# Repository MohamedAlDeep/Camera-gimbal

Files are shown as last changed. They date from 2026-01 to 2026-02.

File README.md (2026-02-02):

# HL Camera Gimbal
This is 3-Axis camera gimbal capable of lifting medium weight mirrorless cameras thus the *HL (heavy lifter)*, this product features two intertial units eliminating fast movement drifting. 

> Why making this project?

First it is cooolll in my oppinion, second I found that this would be integrated into other future projects not with the same frame but with the pcb, also My brother owns a camera.

## Wiring Diagram
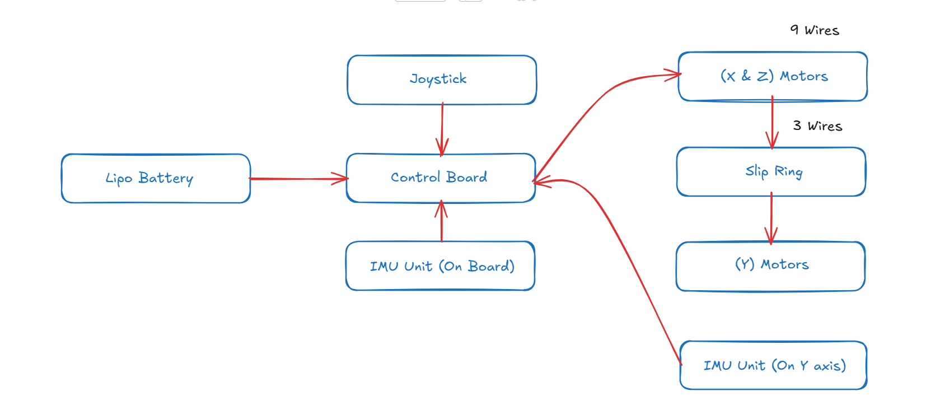
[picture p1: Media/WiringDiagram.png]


## BOM
| Name | Description | Link | Unit Price | Quantity | Total | Running Total |
|:---|:---|:---|---:|---:|---:|---:|
| Motors | Rctimer GBM5010-150T 90KV Gimbal Brushless Motor 5010 | [Link](https://ar.aliexpress.com/item/1005002552552208.html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) | 24.99 | 3 | 74.97 | 74.97 |
| Battery | 4S LiPo battery 7.4v  12000mAh 25C | [Link](https://ar.aliexpress.com/item/1005001565460048.html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) | 87.39 | 1 | 87.39 | 162.36 |
| Slip Ring | 5X22mm 6CH 2A | [Link](https://ar.aliexpress.com/item/1005008132607911.html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) | 21.86 | 1 | 21.86 | 184.22 |
| Pin Headers | 1.27mm1*10P Straight Pin header | [Link](https://jlcpcb.com/partdetail/29704-1_27mm1_10P_Straight_Pinheader/C28952) | 0.05 | 2 | 0.1  | 184.32 |
| LED | Small Led for indication | [Link](https://jlcpcb.com/partdetail/Hubei_KENTOElec-KT0603R/C2286) | 0.01 | 1 | 0.01 | 184.33 |
| Resistor 1KΩ | 1k ohm resistor | [Link](https://jlcpcb.com/partdetail/PANASONIC-EXBV4V102JV/C713466) | 0.04 | 3 | 0.12 | 184.45 |
| Resistor 45.3KΩ | 45.3KΩ ohm resistor | [Link](https://jlcpcb.com/partdetail/RALEC-RTT014532FTH/C166189) | 0.01 | 1 | 0.01 | 184.46 |
| Resistor 100KΩ | 100k ohms resistor | [Link](https://jlcpcb.com/partdetail/YAGEO-RC0603FR07100KL/C14675) | 0.01 | 1 | 0.01 | 184.47 |
| Resistor 10KΩ | 10k ohms resistor | [Link](https://jlcpcb.com/partdetail/16079-0603WAJ0103T5E/C15401) | 0.01 | 2 | 0.02 | 184.49 |
| Resistor 2.2KΩ | 2.2K ohms resistor | [Link](https://jlcpcb.com/partdetail/4597-0603WAF2201T5E/C4190) | 0.01 | 2 | 0.02 | 184.51 |
| Capacitor 100μF | 100 micro farads capacitor | [Link](https://jlcpcb.com/partdetail/3153-KM107M063F12RR0VH2FP0/C2772) | 0.05 | 3 | 0.15 | 184.66 |
| Capacitor 10μF | 10 micro farads capacitor | [Link](https://jlcpcb.com/partdetail/20411-CL10A106KP8NNNC/C19702) | 0.01 | 3 | 0.03 | 184.69 |
| Capacitor 0.1μF | 0.1 micro farads capacitor | [Link](https://jlcpcb.com/partdetail/YAGEO-CC0603KRX7R9BB104/C14663) | 0.01 | 3 | 0.03 | 184.72 |
| Toggle Button | Button | [Link](https://jlcpcb.com/partdetail/hanxia-HX_TS4540CJ_160gf022/C7463293) | 0.02 | 1 | 0.02 | 184.74 |
| Motor Drivers | DRV8313PWP | [Link](https://jlcpcb.com/partdetail/TexasInstruments-DRV8313PWPR/C92482) | 1.72 | 3 | 5.16 | 189.9  |
| STM32 Microcontroller | 128Kb memory flash MCU | [Link](https://jlcpcb.com/partdetail/STMicroelectronics-STM32G431CBT6/C529355) | 3.13 | 1 | 3.13 | 193.03 |
| Inductor 10μH | 10μH inductor | [Link](https://jlcpcb.com/partdetail/Sunlord-SDFL1608S100KTF/C1035) | 0.01 | 1 | 0.01 | 193.04 |
| Power converter | TPS54302 | [Link](https://jlcpcb.com/partdetail/TexasInstruments-TPS54302DDCR/C311983) | 0.15 | 1 | 0.15 | 193.19 |
| Inertial Units | ICM-20602 | [Link](https://jlcpcb.com/partdetail/TDKInvenSense-ICM20602/C97633) | 5.08 | 2 | 10.16 | 203.35 |
## Showcase

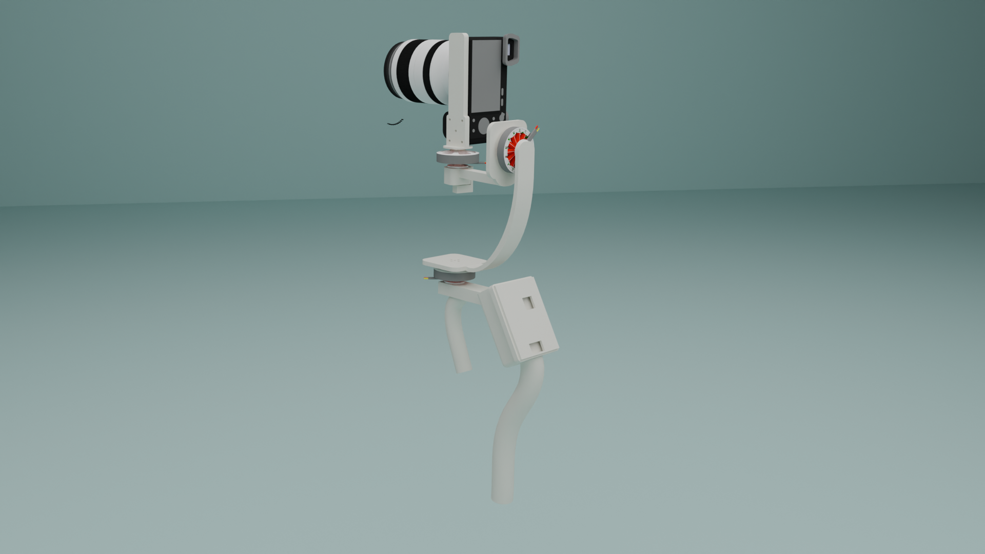
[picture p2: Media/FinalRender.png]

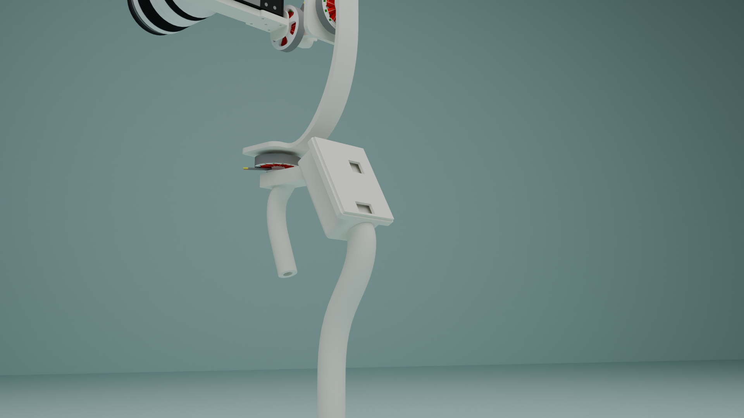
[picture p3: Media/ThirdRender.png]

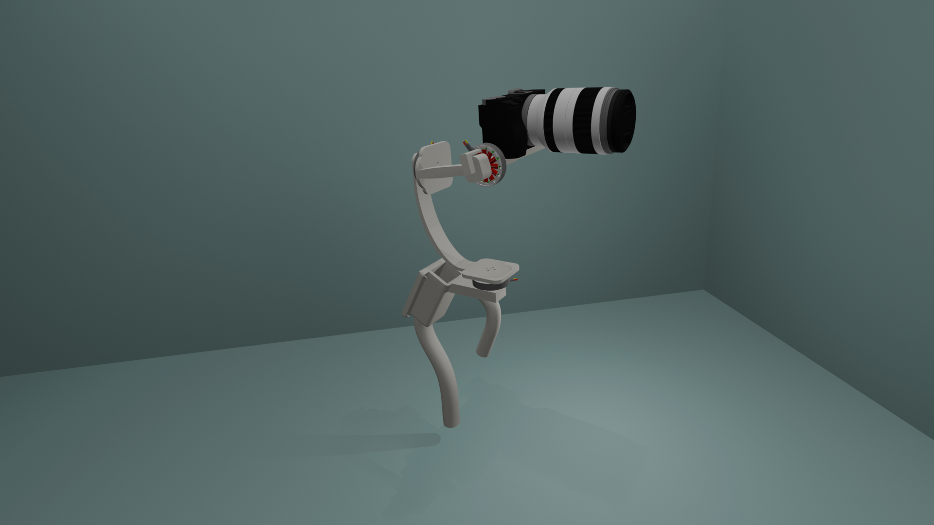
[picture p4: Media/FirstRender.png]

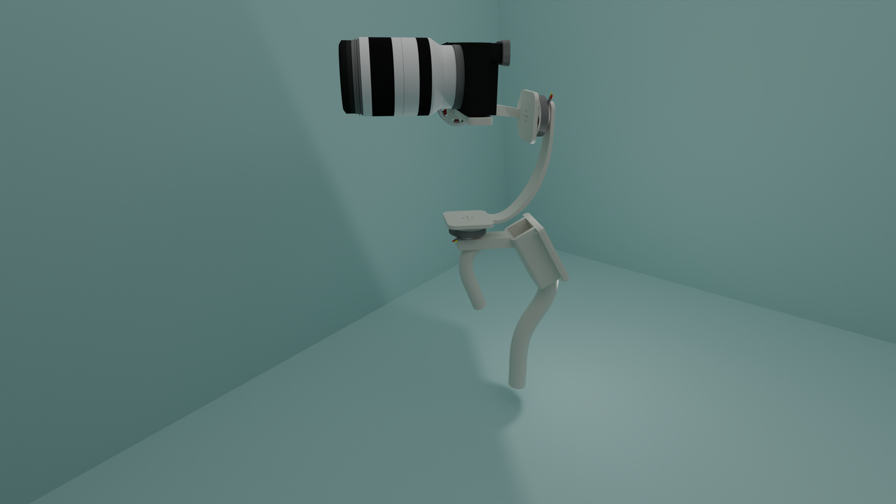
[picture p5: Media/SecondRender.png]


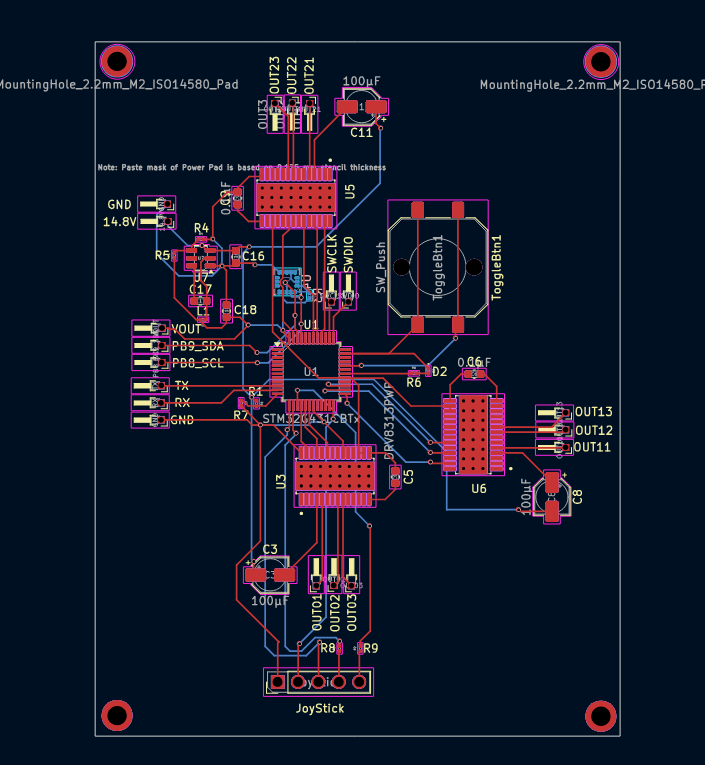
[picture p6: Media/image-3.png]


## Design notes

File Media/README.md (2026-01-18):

# HL Camera Gimbal
This is 3-Axis camera gimbal capable of lifting medium weight mirrorless cameras thus the *HL (heavy lifter)*, this product features two intertial units eliminating fast movement drifting. 

> Why making this project?

I found that this would be integrated into other future projects, also My brother owns a camera and.

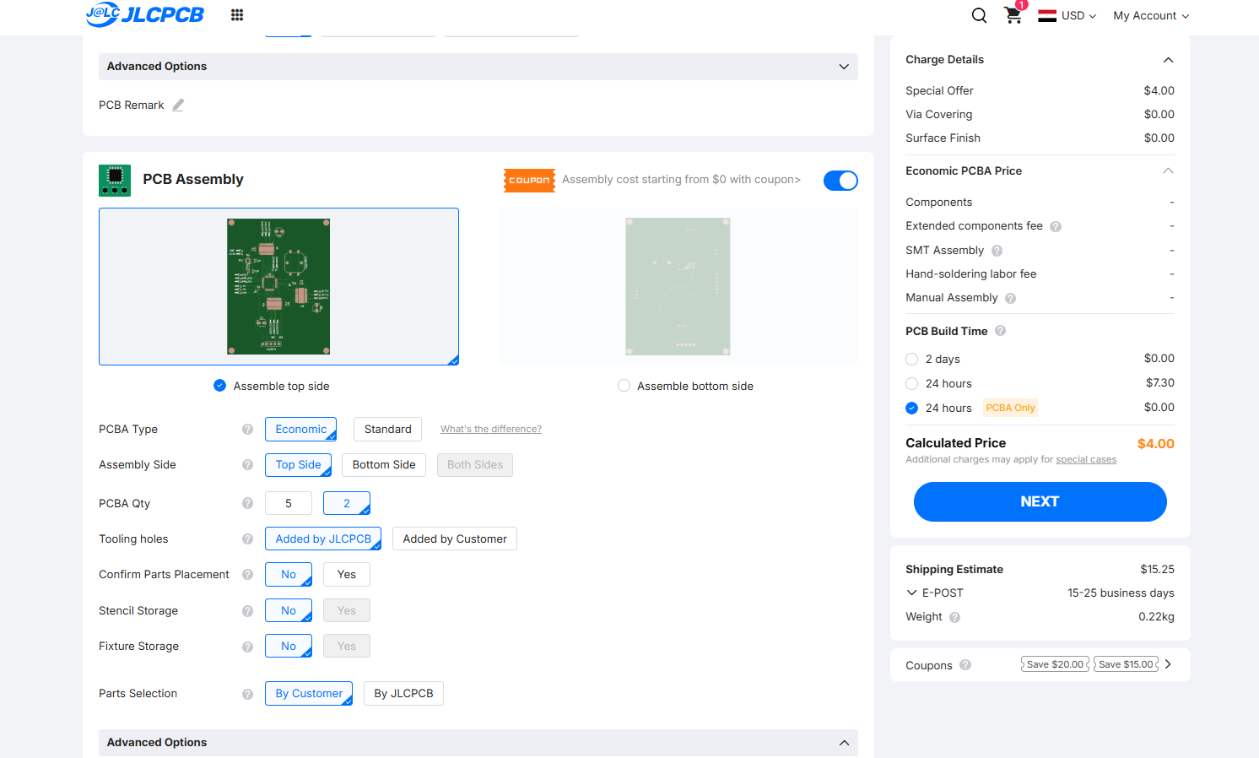
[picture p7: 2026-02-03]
Media/CARTS/JLC_PCB_CART.png

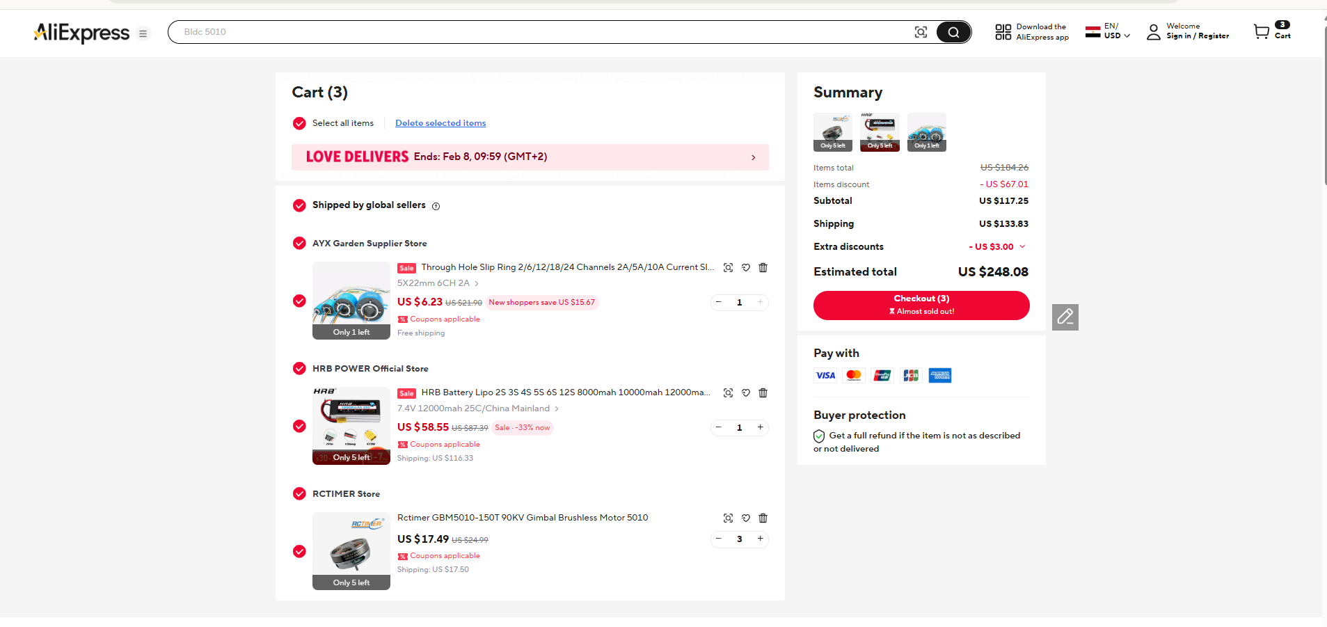
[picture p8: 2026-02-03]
Media/CARTS/AliExpressCart.png

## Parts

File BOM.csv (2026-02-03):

Name | Description | Link | Unit Price | Quantity | Total | Running Total
Motors | Rctimer GBM5010-150T 90KV Gimbal Brushless Motor 5010 | https://ar.aliexpress.com/item/1005002552552208.html?curPageLogUid=78YJsnV9XrQS | 24.99 | 3 | 74.97 | 74.97
Battery | 4S LiPo battery 7.4v 12000mAh 25C | https://ar.aliexpress.com/item/1005001565460048.html?curPageLogUid=I0zJC1hyaeP7 | 87.39 | 1 | 87.39 | 162.36
Slip Ring | 5X22mm 6CH 2A | https://ar.aliexpress.com/item/1005008132607911.html?curPageLogUid=WKGMTuvrKkpL | 21.86 | 1 | 21.86 | 184.22
Pin Headers | 1.27mm1*10P Straight Pin header | https://jlcpcb.com/partdetail/29704-1_27mm1_10P_Straight_Pinheader/C28952 | 0.05 | 2 | 0.1 | 184.32
LED | Small Led for indication | https://jlcpcb.com/partdetail/Hubei_KENTOElec-KT0603R/C2286 | 0.01 | 1 | 0.01 | 184.33
Resistor 1KΩ | 1k ohm resistor | https://jlcpcb.com/partdetail/PANASONIC-EXBV4V102JV/C713466 | 0.04 | 3 | 0.12 | 184.45
Resistor 45.3KΩ | 45.3KΩ ohm resistor | https://jlcpcb.com/partdetail/RALEC-RTT014532FTH/C166189 | 0.01 | 1 | 0.01 | 184.46
Resistor 100KΩ | 100k ohms resistor | https://jlcpcb.com/partdetail/YAGEO-RC0603FR07100KL/C14675 | 0.01 | 1 | 0.01 | 184.47
Resistor 10KΩ | 10k ohms resistor | https://jlcpcb.com/partdetail/16079-0603WAJ0103T5E/C15401 | 0.01 | 2 | 0.02 | 184.49
Resistor 2.2KΩ | 2.2K ohms resistor | https://jlcpcb.com/partdetail/4597-0603WAF2201T5E/C4190 | 0.01 | 2 | 0.02 | 184.51
Capacitor 100μF | 100 micro farads capacitor | https://jlcpcb.com/partdetail/3153-KM107M063F12RR0VH2FP0/C2772 | 0.05 | 3 | 0.15 | 184.66
Capacitor 10μF | 10 micro farads capacitor | https://jlcpcb.com/partdetail/20411-CL10A106KP8NNNC/C19702 | 0.01 | 3 | 0.03 | 184.69
Capacitor 0.1μF | 0.1 micro farads capacitor | https://jlcpcb.com/partdetail/YAGEO-CC0603KRX7R9BB104/C14663 | 0.01 | 3 | 0.03 | 184.72
Toggle Button | Button | https://jlcpcb.com/partdetail/hanxia-HX_TS4540CJ_160gf022/C7463293 | 0.02 | 1 | 0.02 | 184.74
Motor Drivers | DRV8313PWP | https://jlcpcb.com/partdetail/TexasInstruments-DRV8313PWPR/C92482 | 1.72 | 3 | 5.16 | 189.9
STM32 Microcontroller | 128Kb memory flash MCU | https://jlcpcb.com/partdetail/STMicroelectronics-STM32G431CBT6/C529355 | 3.13 | 1 | 3.13 | 193.03
Inductor 10μH | 10μH inductor | https://jlcpcb.com/partdetail/Sunlord-SDFL1608S100KTF/C1035 | 0.01 | 1 | 0.01 | 193.04
Power converter | TPS54302 | https://jlcpcb.com/partdetail/TexasInstruments-TPS54302DDCR/C311983 | 0.15 | 1 | 0.15 | 193.19
Inertial Units | ICM-20602 | https://jlcpcb.com/partdetail/TDKInvenSense-ICM20602/C97633 | 5.08 | 2 | 10.16 | 203.35
Delivery
PCB |  |  |  |  |  | 15.25
ALI Express |  |  |  |  |  | 133.8
Total |  |  |  |  |  | 352.4

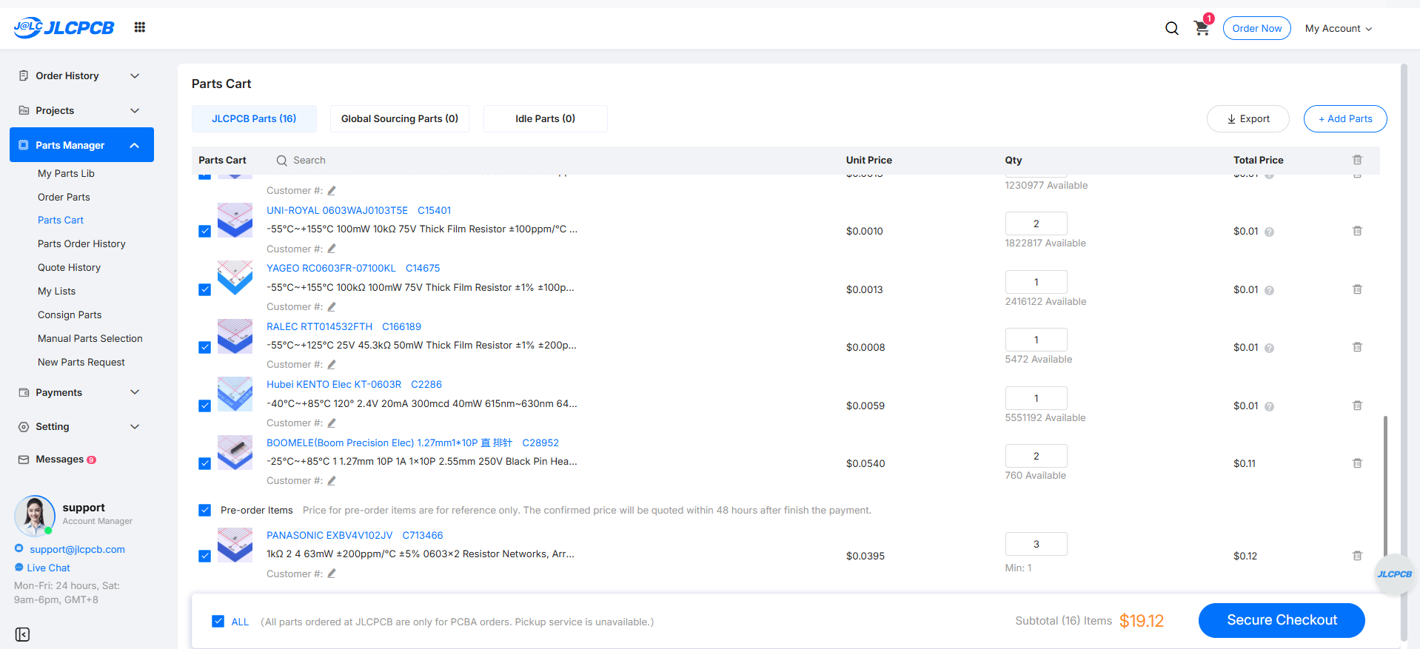
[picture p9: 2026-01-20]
Media/CARTS/JLC_Components_Cart.png

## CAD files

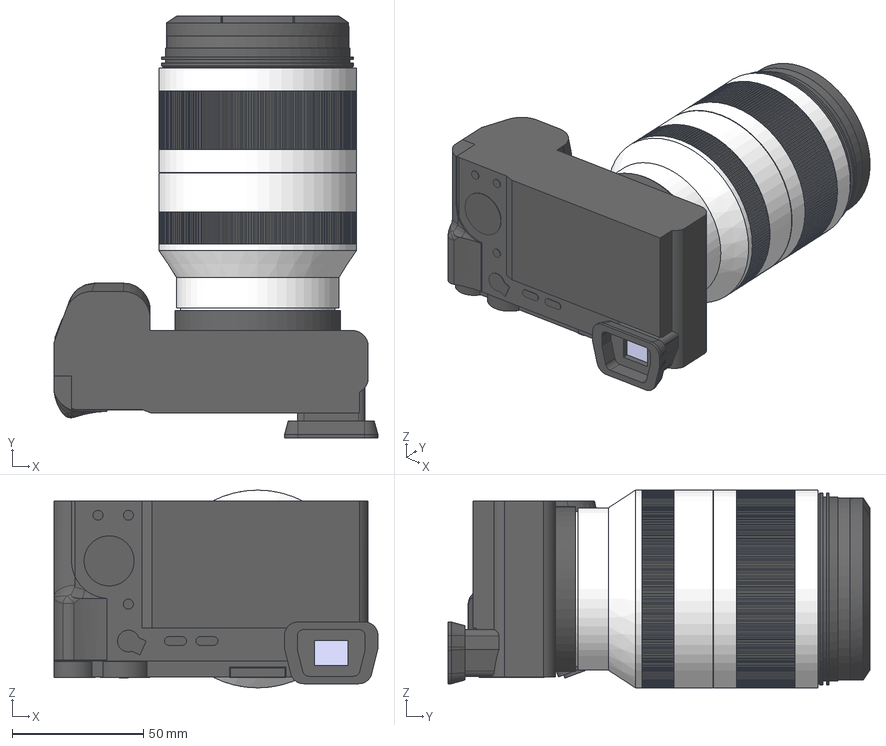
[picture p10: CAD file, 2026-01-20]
CAD/Prebuilt_Modules/A6300 18 200 Assembly.stp
123.2 x 160.4 x 75.2 mm
SEL 18 200
A6300
UV Filter
Lens Cap

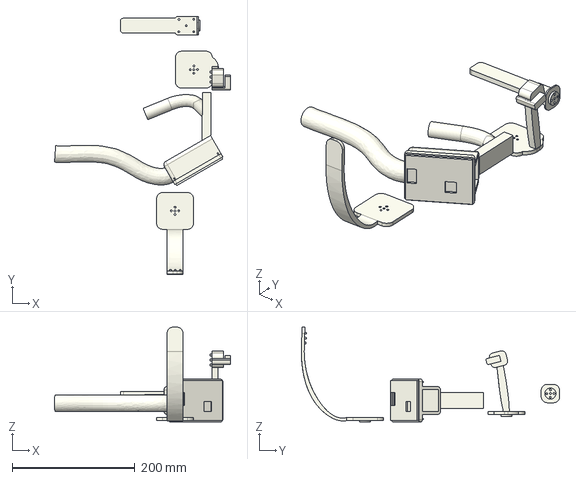
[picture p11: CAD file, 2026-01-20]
CAD/Frame_3DPrint.step
286.4 x 420.3 x 154.1 mm

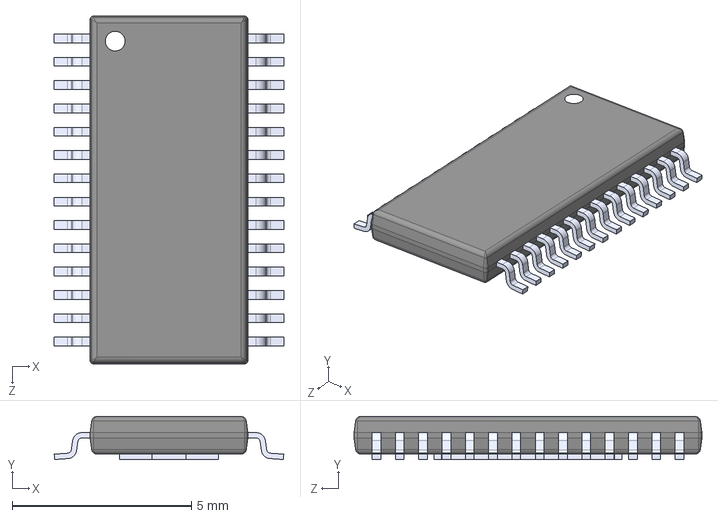
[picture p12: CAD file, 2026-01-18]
PCB/PrerequisitesFootprints/DRV8313PWP.step
6.40 x 1.20 x 9.70 mm

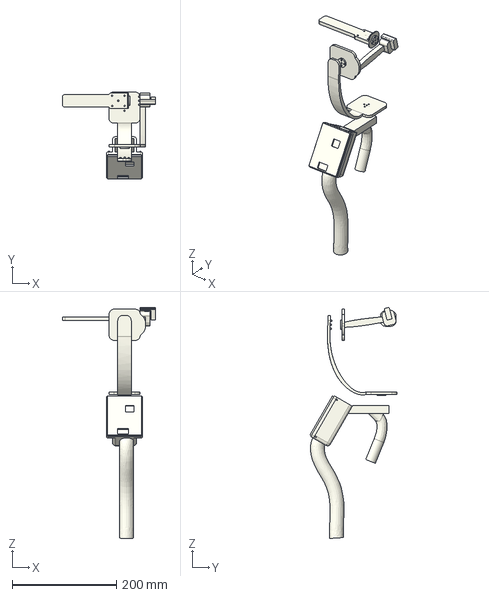
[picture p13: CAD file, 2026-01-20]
CAD/Frame_Parts_NONSetup.step
179.4 x 167.4 x 443.6 mm

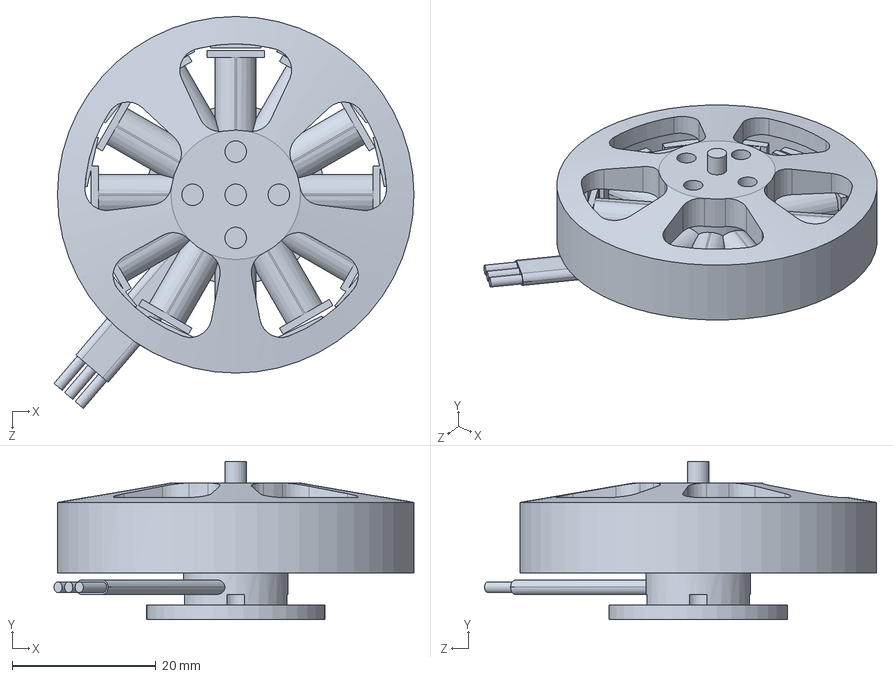
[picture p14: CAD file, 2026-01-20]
CAD/Prebuilt_Modules/BLDC_Motor_5010.SLDPRT
50.1 x 22.0 x 54.5 mm

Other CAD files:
CAD/Render.blend

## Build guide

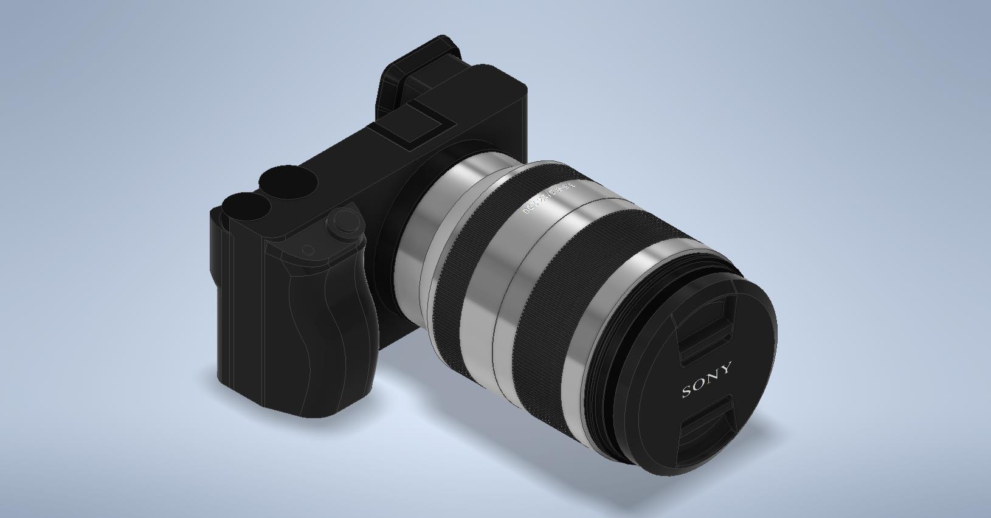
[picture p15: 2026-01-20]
CAD/Prebuilt_Modules/A6300 18 200 Assembly.jpg

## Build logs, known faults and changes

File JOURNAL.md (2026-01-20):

# Journal
Total time spent: 29.5 hours

## Defining Structure
> 18/1/2026

> Time: 4h

I need this gimbal to be used with medium mirrorless cameras which usally weight 1kg-2kg, so that is the goal.

The components are as the folling 
1. Control board
    - Custom built
2. Motors 
    - 3x 90kv Brushless motors 
3. Sensor 
    - Using two ICM20602 (inertial sensors) for minimizing yaw drift with fast movement
4. Frame
    - Considering minimizing the frame to make the product much compact
5. Battery
    - Using 4S LiPo battery

### Control board 
The board would feature the following 
- Power Button
- Toggle Button for Manual movement 
- Analog Joystick
- Two Buttons for joystick sensitivity 

In this board i am using the following components
- STM32G431 
- DRV8313 three phase driver for each motor
- TPS54302 step down converter

Firmware setup
- SimpleFOC library

## Schematic 
> 18/1/2026

> Time: 4h

I use Kicad in my design.

The first thing i added the schematic symbol for the STM32 then added the ones for IMU, for the DRV8313 driver i had to download the footprint and symbol from SnapMagic site and imported them to kicad then started connecting main connections for the STM32, then went for buck converter connections from the datasheet, then made connections for the IMU's connection, then connections for the drivers.

Next i would add the buttons and joystick.



## Additionals for Schematic & PCB
> 19/1/2026

> Time: 2h

I started with adding the pcb buttons i listed before, one switch for toggeling the gimbal on or off then added five connection pins for joystick module, i found it simpler to use an already made joystick pcb than 3d printing it.

Second section i organized the schematic by putting the motor drivers on a separate sheet. 

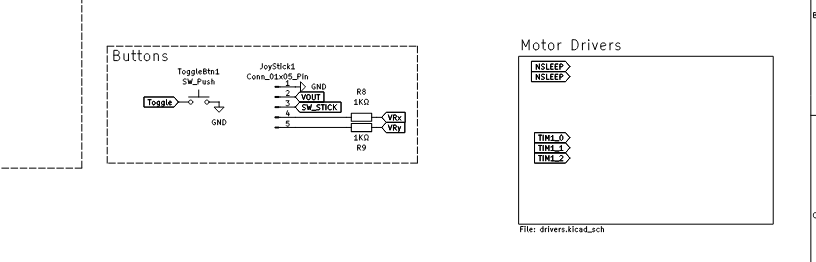
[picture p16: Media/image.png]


Then i worked on assigning footprints for each component, i encountered issue for the imported motor driver footprint as i imported it with different name and the library i imported was almost messed up so had to reimport that check the footprint.

## Schematic Revisions
> 19/1/2026

> Time: 2h

Once all that was done i went for pcb editor and got all the components together started getting each component into its respective place and i wanted to make a 4 layered pcb as for reducing the size, but i thought this is my first prototype and it would be overkill if i started with 4 layers so i went for the normal 2 layer setup.

After i was organizing the pcb components i found the connection pins on the drivers did have their reference names on the schematic but not on the silkscreen so i went back to the schematic changed their names and got them in what you see in the image, `OUTx_Z` is naming convention like number pairs describing each three output for each motor.

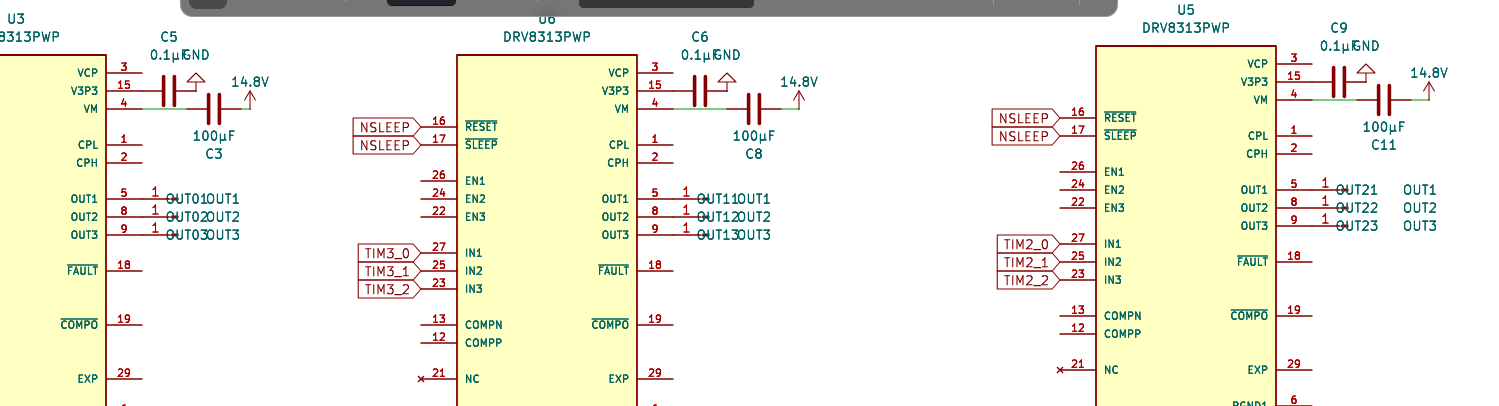
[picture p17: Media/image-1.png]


## Connecting PCB 
> 19/1/2026

> Time: 4h

So after organizing the pcb, i started connecting the rat lines of each driver alone making the mess a little easier to deal with then after that, then working on putting all of them together which took endless times, i wanted to connect the drivers in series so the board is narrower but again, it is only possible with a 4 layer board and even with this i was able to put sloppy cross connections with lots of vias and then i connected the buck converter and added the two `GND` & `14.8V` pins which are directly connected to the battery. 

After connecting the things together i found that i had to probably chose a little smaller button for the toggle on/off as this is taking a lot of space i am putting this into consideration for future versions.

The final steps was adding the outer border for pcb frame and the mounting holes 



## Frame & CAD setup
> 19/1/2026

> Time: 1h

After finishing the pcb i exported it as `.step` for importing in Fusion 360, so to start off the first thing is having a holder case for the pcb, so i made some sketches and doing cad things, so the final result i got was what you see in the image, i know it looks simple but again i think organizing that should be in future iterations, 

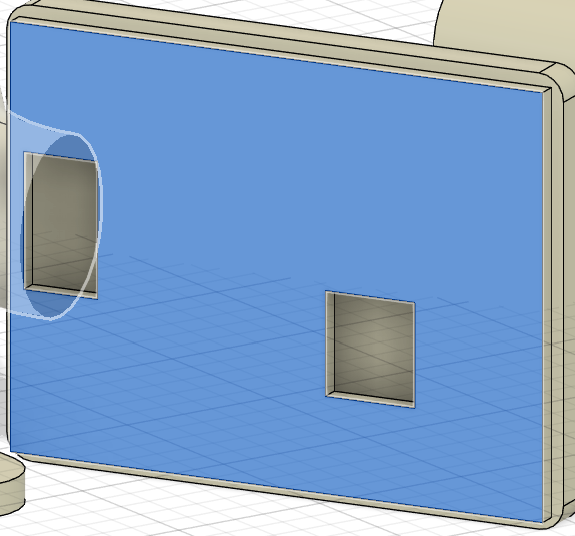
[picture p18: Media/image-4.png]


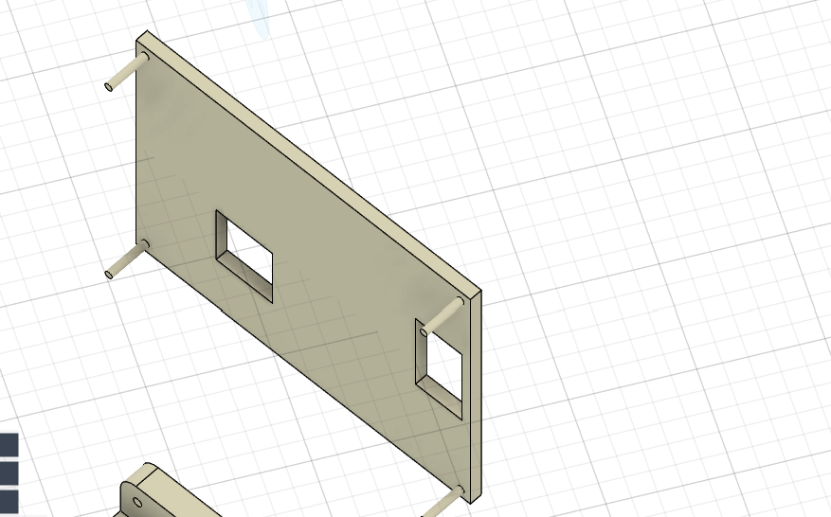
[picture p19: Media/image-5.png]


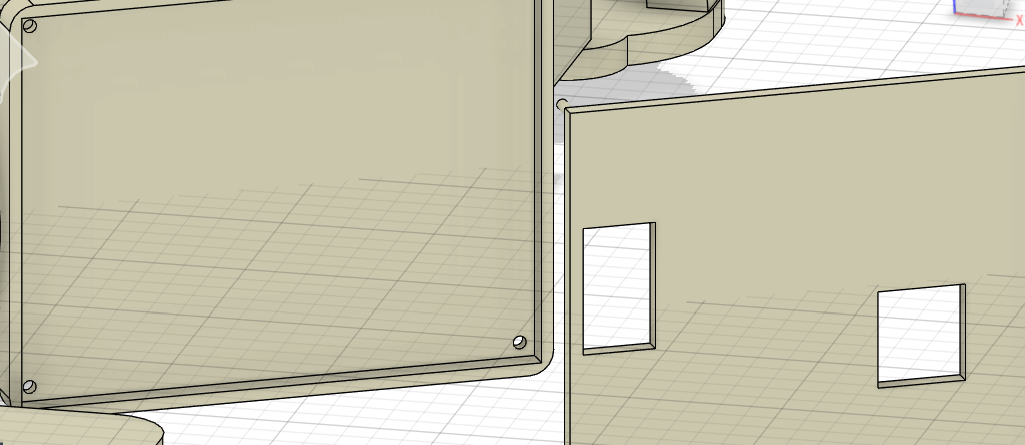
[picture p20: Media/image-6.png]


## General Frame & Ergonomics
> 20/1/2026

> Time: 1h

So i have chosen somewhat of a big battery so i need a big place to put them, i took the battery dimensions for the Aliexpress seller (link in BOM) and made a case behind the original pcb holder because that is the only place i found intuative.

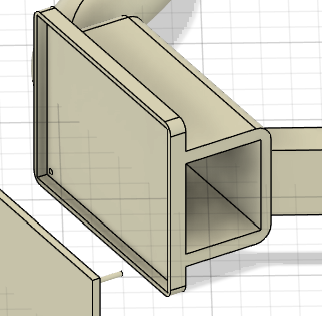
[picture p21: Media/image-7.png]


## Handles 
> 20/1/2026

> Time: 3h

After that i thought about how to handle that large structure and i got inspired by some professional gimbals and i tried my best, at first i made a simple hand drawn 2D cross section imagining how the handles would be and yeah almost every large gimbal use two handle setup as it would be hard for a person to hold that weight comfortably with one hand.

What you see in the image as blue are the main frames while the red circles are the rotating motors, if you notice that thing on the green line is the imported step file for the pcb.

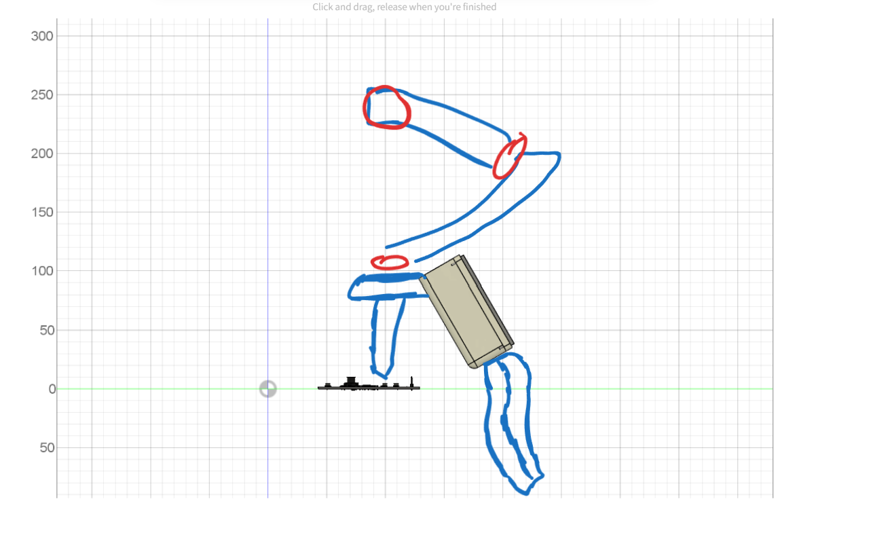
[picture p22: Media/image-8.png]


So The next step is taking that image to reality,
i took somewhat medium level approach in making the handles as they are complex curved geometry.

So i made a curved path and used the Fusion 360 tool "pipe" for making the pipe shape that you see in the next image, the process was tedious becuase somehow the software doesn't accept the fact that i want to increase the diameter of the handler and i couldn't resolve that issue and i still don't know why, i would like to improve that in future iterations and maybe would try to get help from a professional. However the second handle was much better as also somehow i was able to get large diameter for the second top handle.

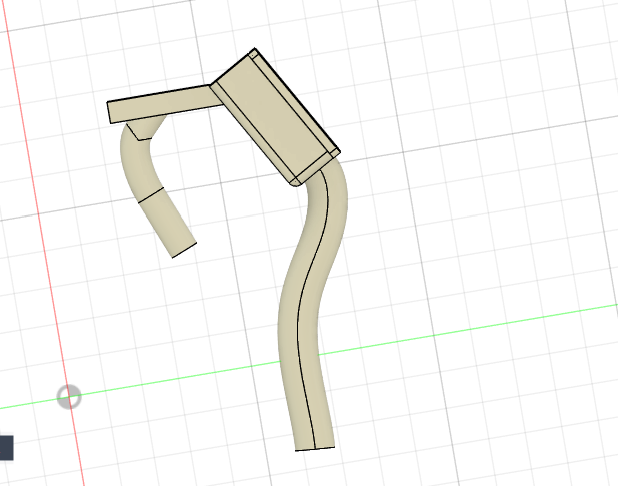
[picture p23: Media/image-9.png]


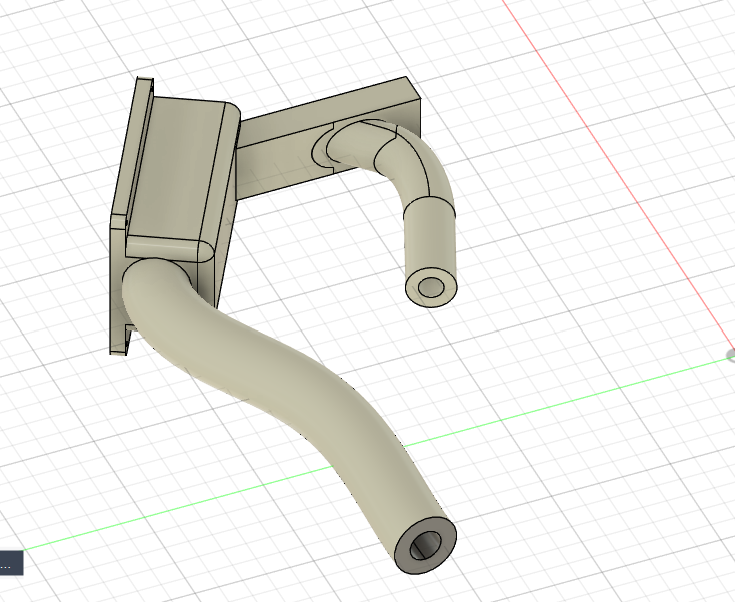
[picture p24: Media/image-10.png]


I thought about adding a rough texture to the handles but it was too much for my skills, so i was good with that. 

## Motor Holders
> 20/1/2026

> Time: 3h

Starting with the first motor i searched for an existing cad model for my BLDCs and i found the one you see in the image colored as green, the next part was the most exhausting as i had to be creative, at first i made a circular base which took time found that i can't make a model for the parts connected to the motor base as circular geometry was too complicated so i had to roll back and design from the begining the base with square shape and gave it rounded edges, then started making the curved path of the holder that connects the other motors. 

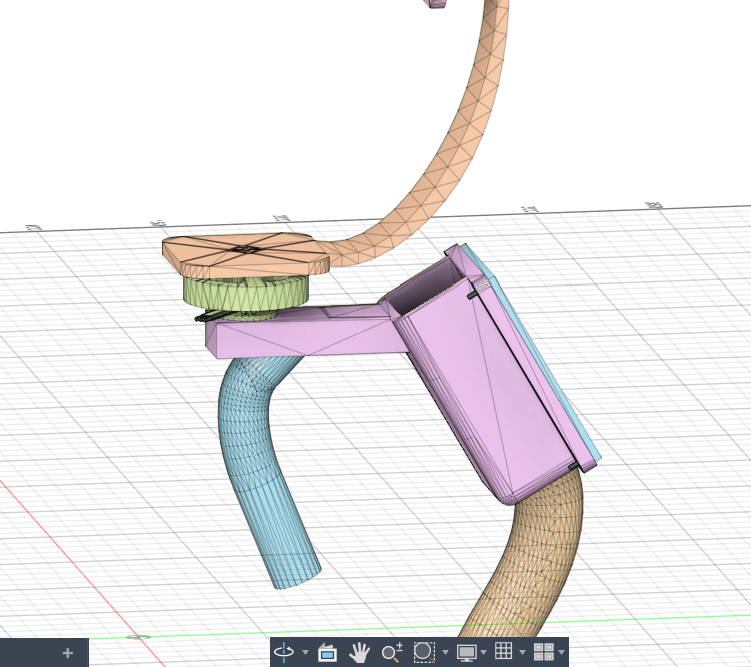
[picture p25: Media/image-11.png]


## Seconds motors
> 20/1/2026

> Time: 2h

Here i continued the curved geometry and built the second motor base on it, which is directly horizontal, then i made the perpendicular structure that holds the third motor.  
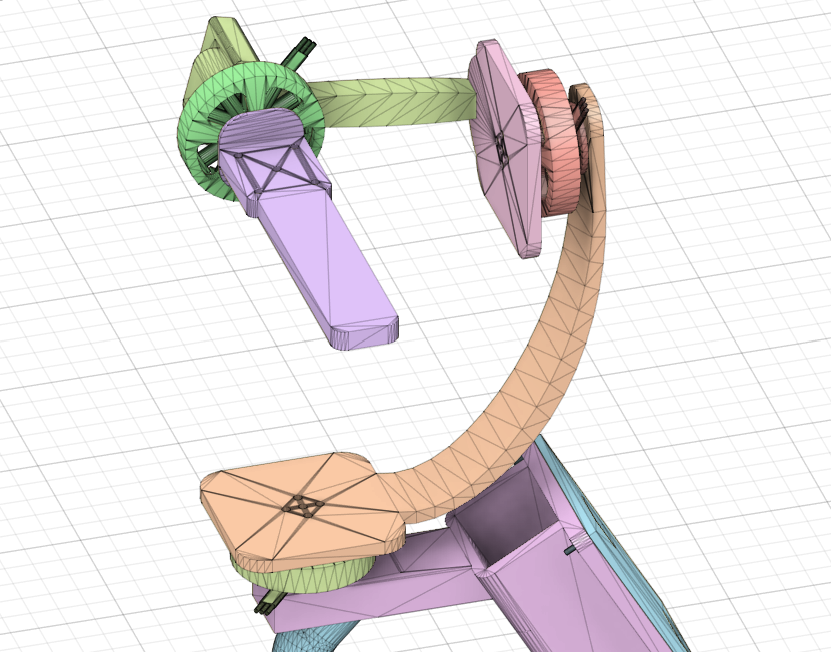
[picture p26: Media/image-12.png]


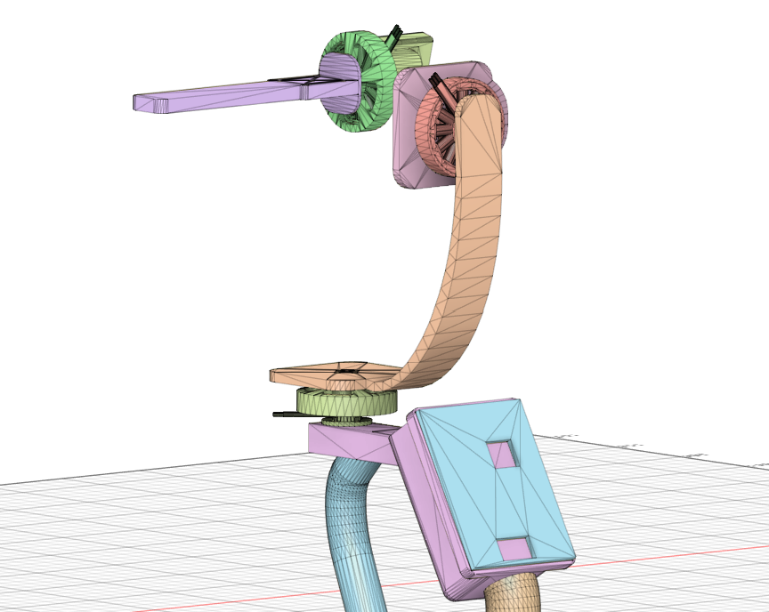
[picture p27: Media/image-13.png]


When making the third motor i realised i needed some way of "equalizing" or centering the *center of mass* of the device so i added the part you see that is highlighted with red strokes, that part can be removed and i am planning on making it hold counter weights, the last part was the camera holder which is a simple rectangular shape, i added four screw parts for the wider first segment of that rectangle.  

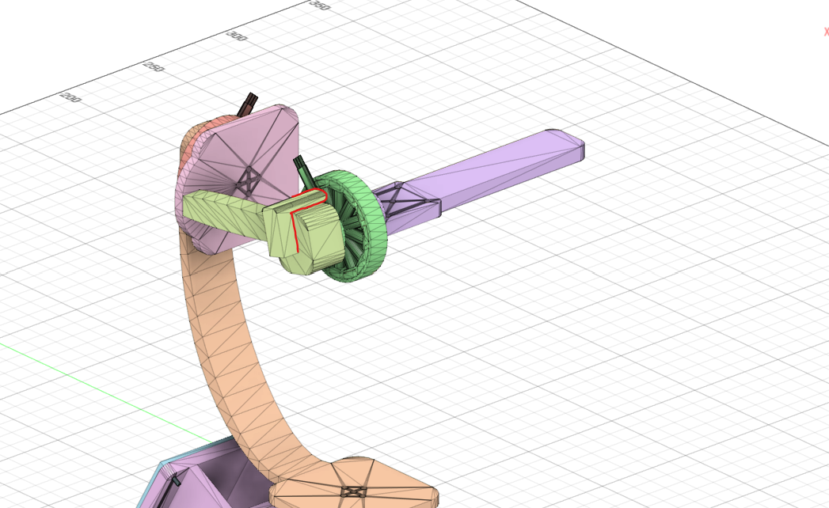
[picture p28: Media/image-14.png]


## Final thoughts
> 20/1/2026

> Time: 30mins

I added camera model for the sake of rendering cool images, and most importantly checking how the whole frame looks. 

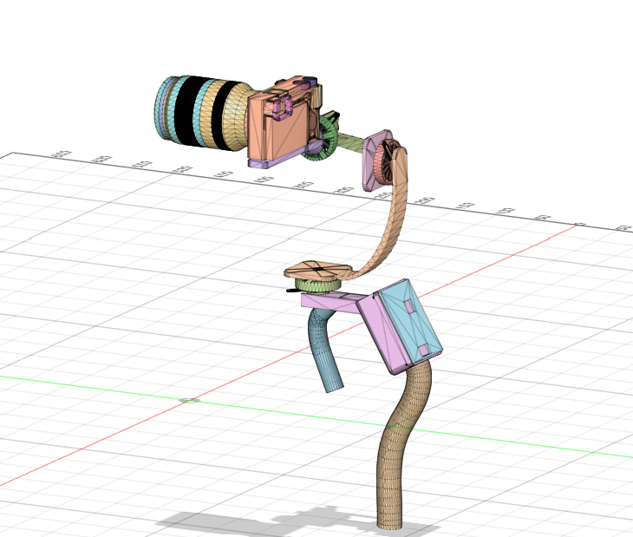
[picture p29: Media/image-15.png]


Here i added fillets (rounded edges) for the bottom parts of both handles making it look a little professional,   

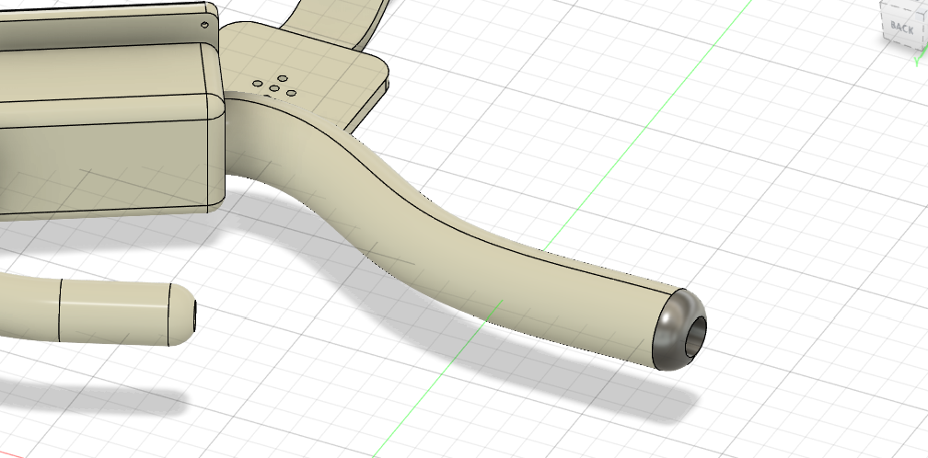
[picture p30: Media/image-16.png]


Also added a fillet to the edge of the first motor base.

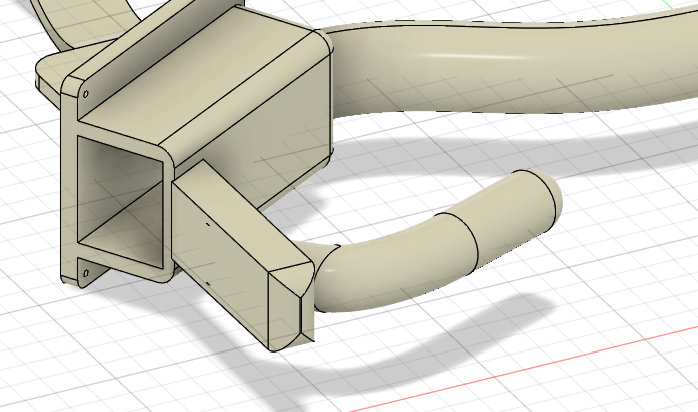
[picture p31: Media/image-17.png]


## Rendering
> 20/1/2026

> Time: 30mins

I exported the design into `.step` and `.obj` for blender for rendering, i am not good at rendering but got the next images, i had bad lighting for the first two images, but got much better at the third.

I think i would do an animation that shows the gimbal moving which would be cool but i should fix the rendering first.





## BOM & Submission
> 20/1/2026

> Time: 2h

So the most exhausting process **ever**, i organized all components of pcb together and put them in one excel sheet then open JLCPCB components library and querry each components, make sure it is the correct one and then taking its link and part number, after all that i start making new sheet in which it is much cleaned one with prices of each and you can see that in `PCB` folder, then after that i took each component and got the important data only from it and putting it into the main `BOM.csv` giving you the final addition you see in the `Readme`.

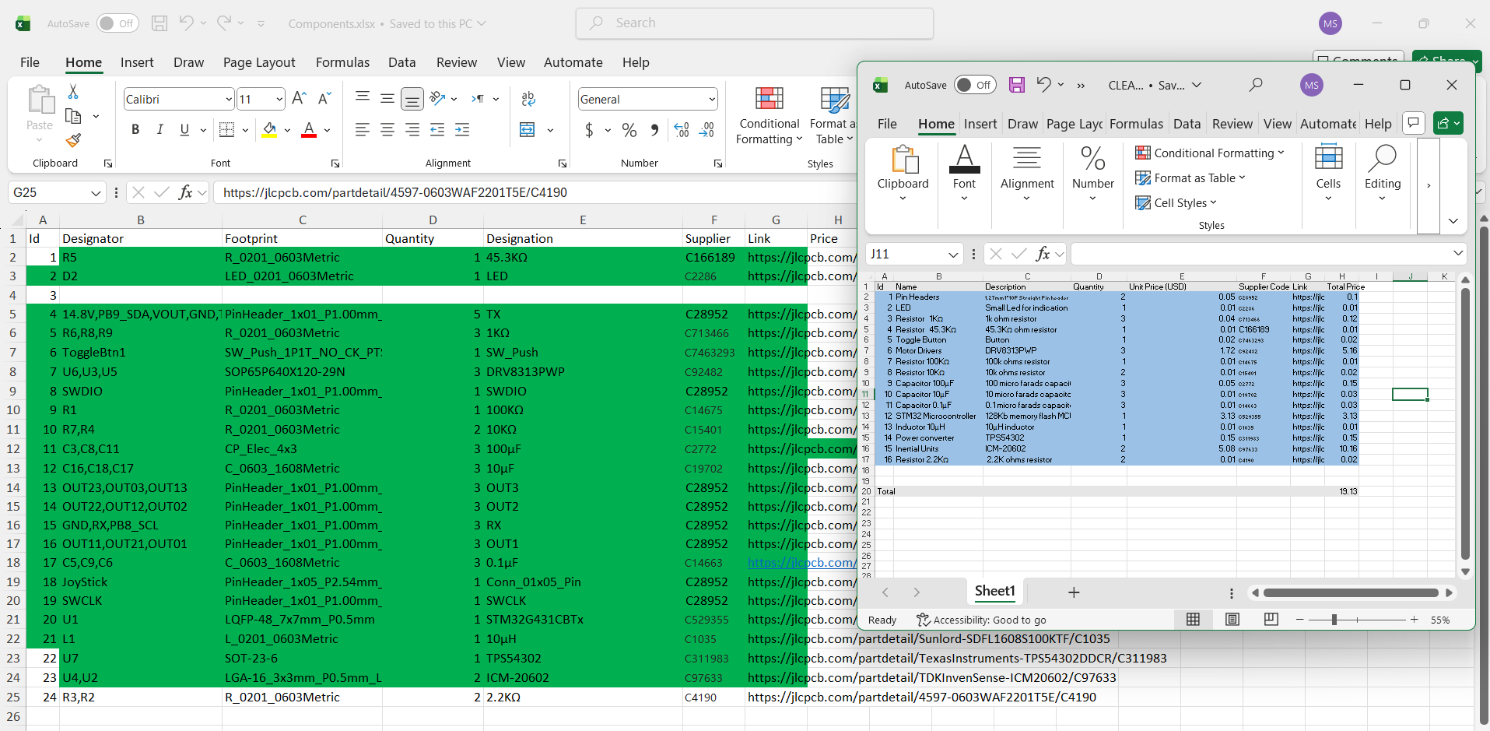
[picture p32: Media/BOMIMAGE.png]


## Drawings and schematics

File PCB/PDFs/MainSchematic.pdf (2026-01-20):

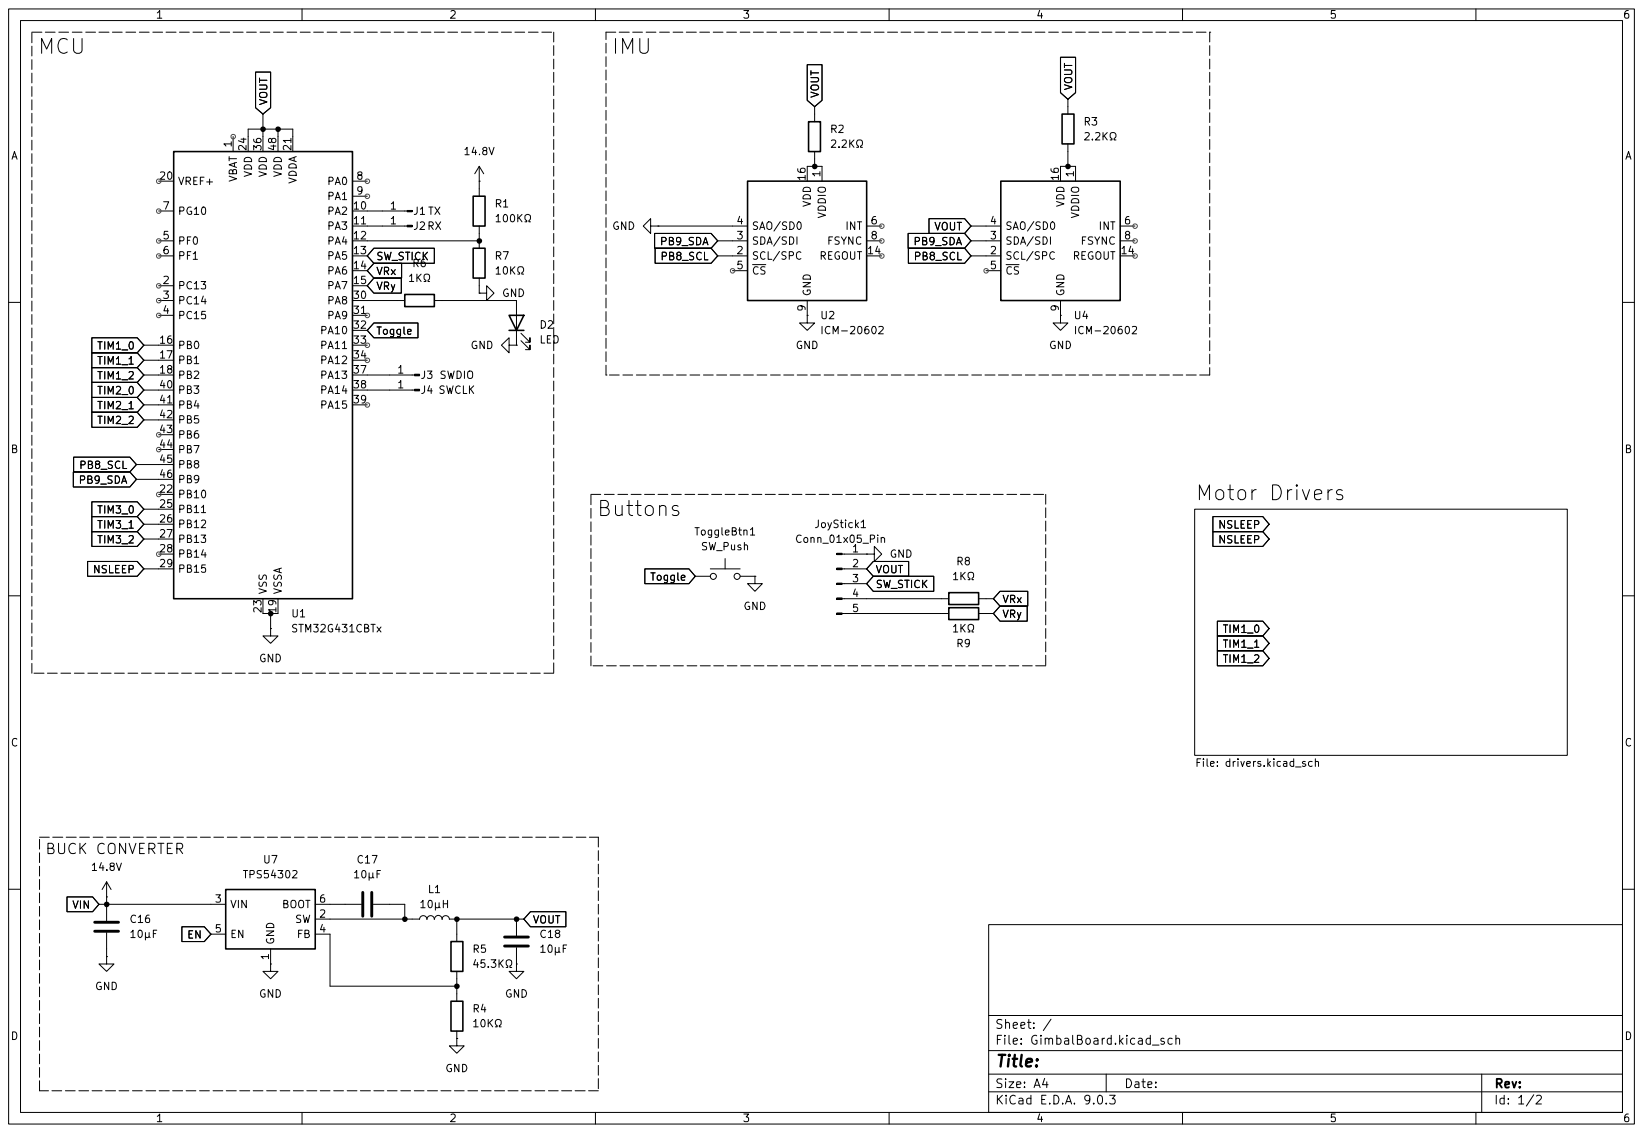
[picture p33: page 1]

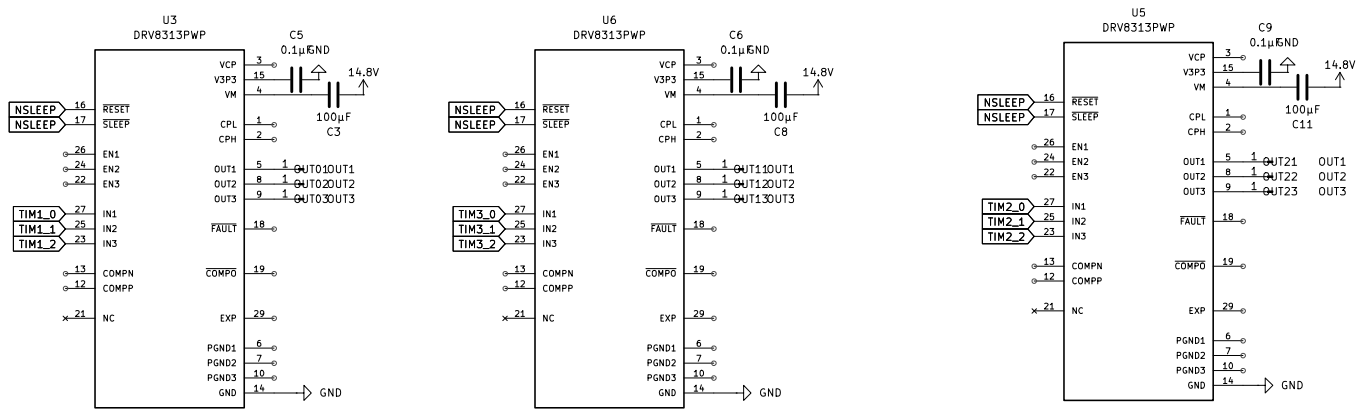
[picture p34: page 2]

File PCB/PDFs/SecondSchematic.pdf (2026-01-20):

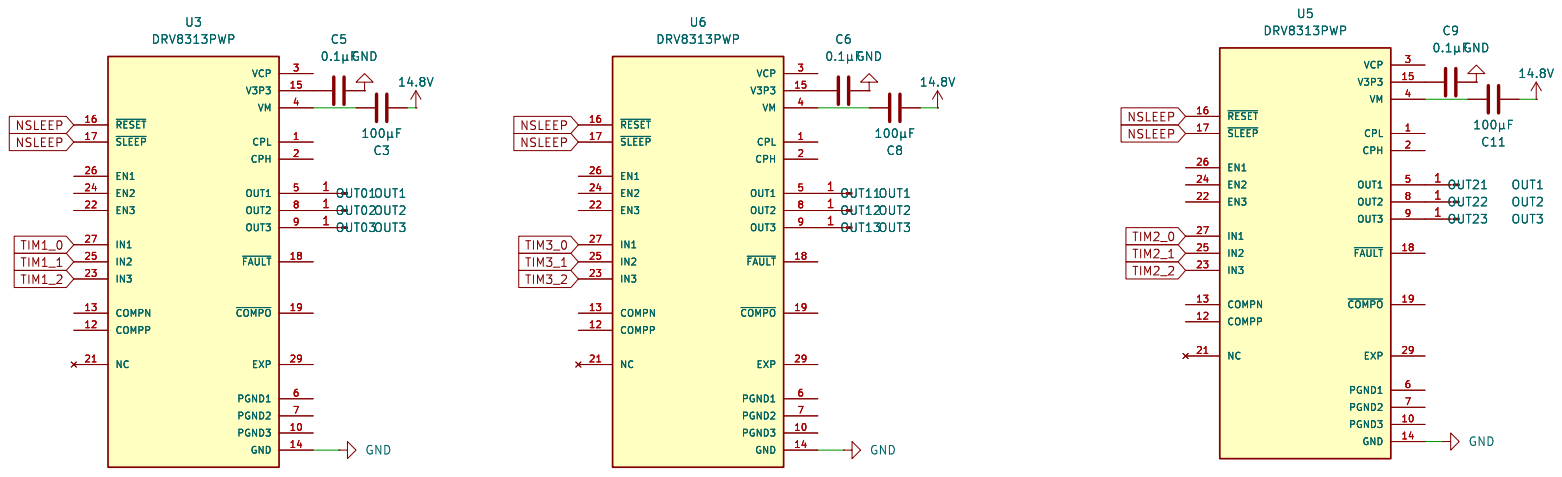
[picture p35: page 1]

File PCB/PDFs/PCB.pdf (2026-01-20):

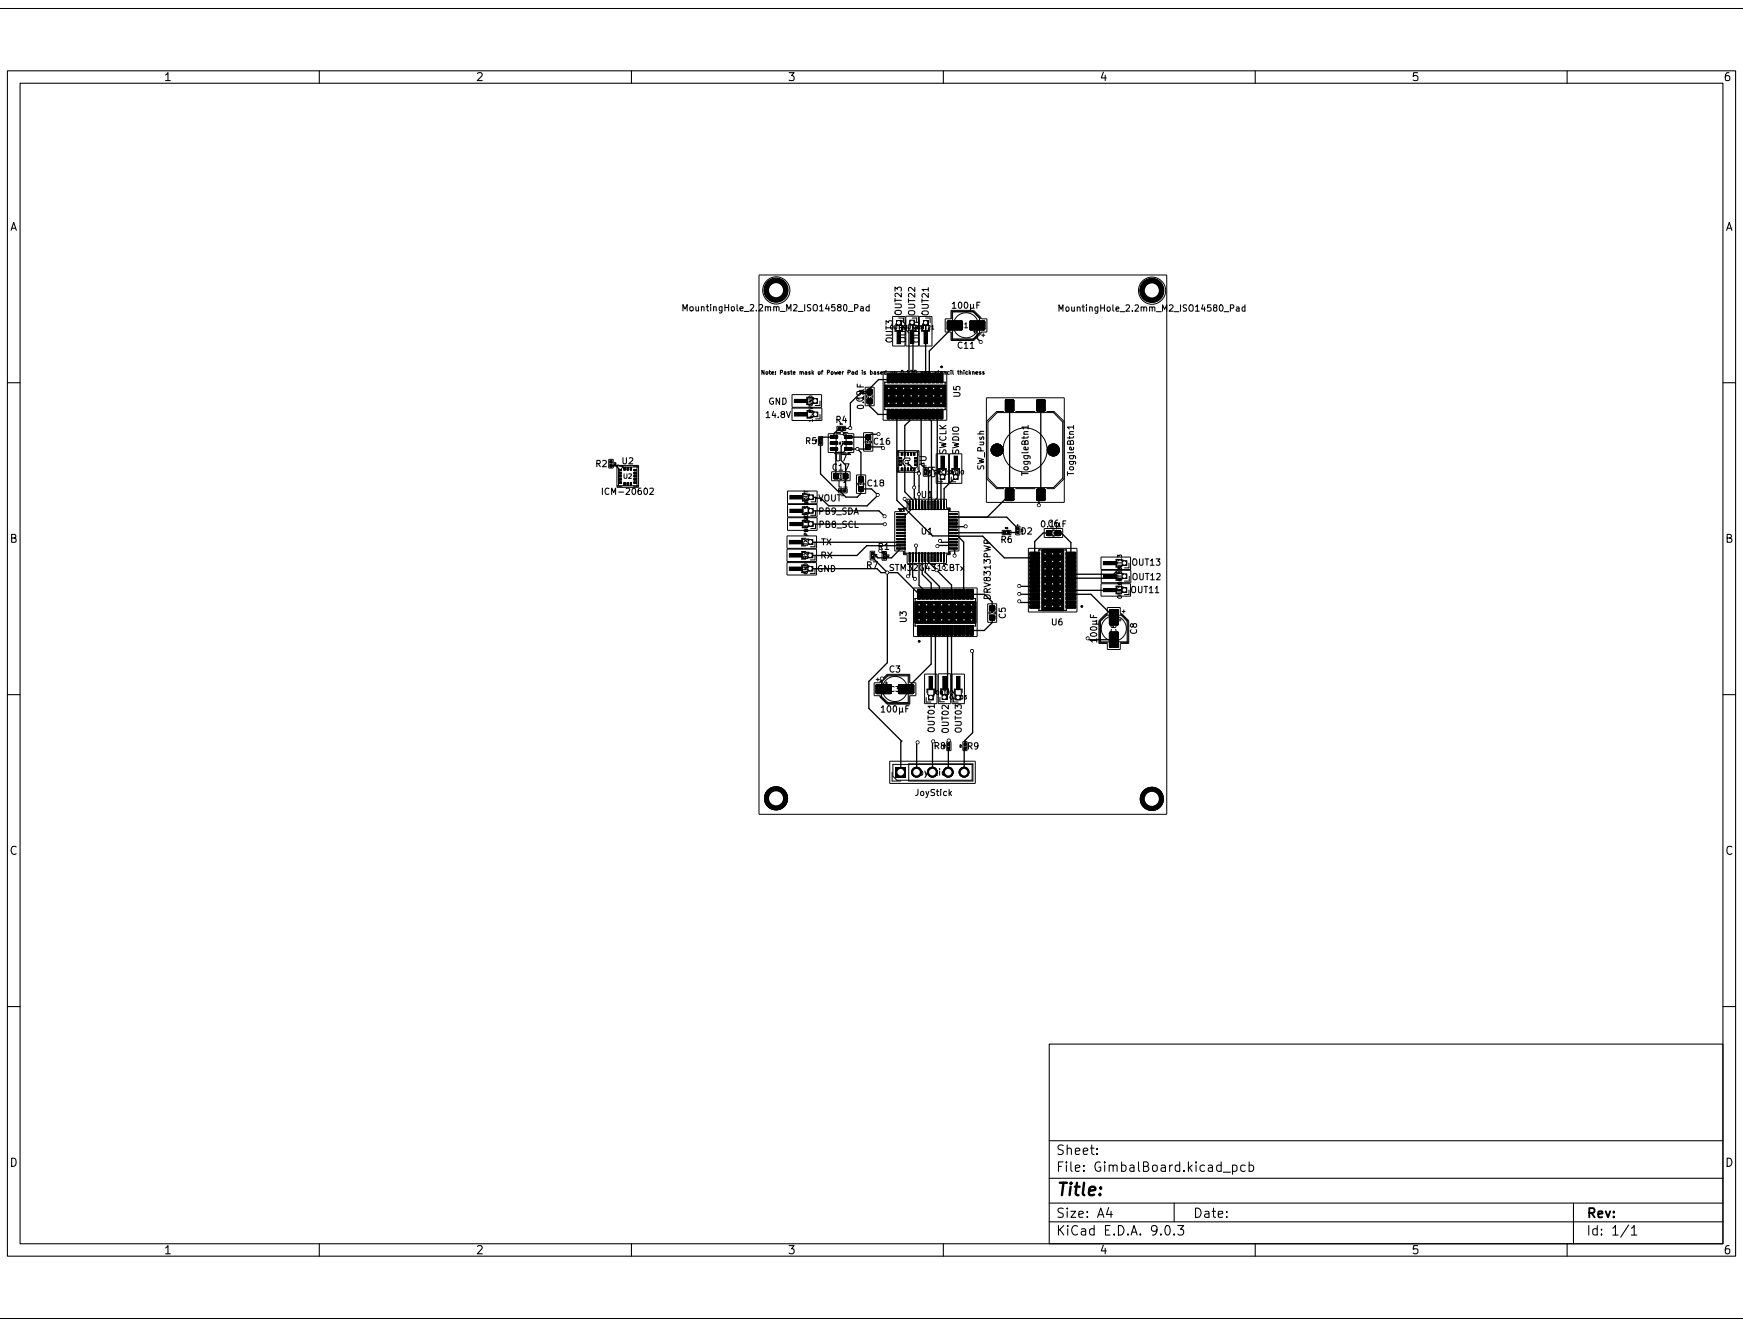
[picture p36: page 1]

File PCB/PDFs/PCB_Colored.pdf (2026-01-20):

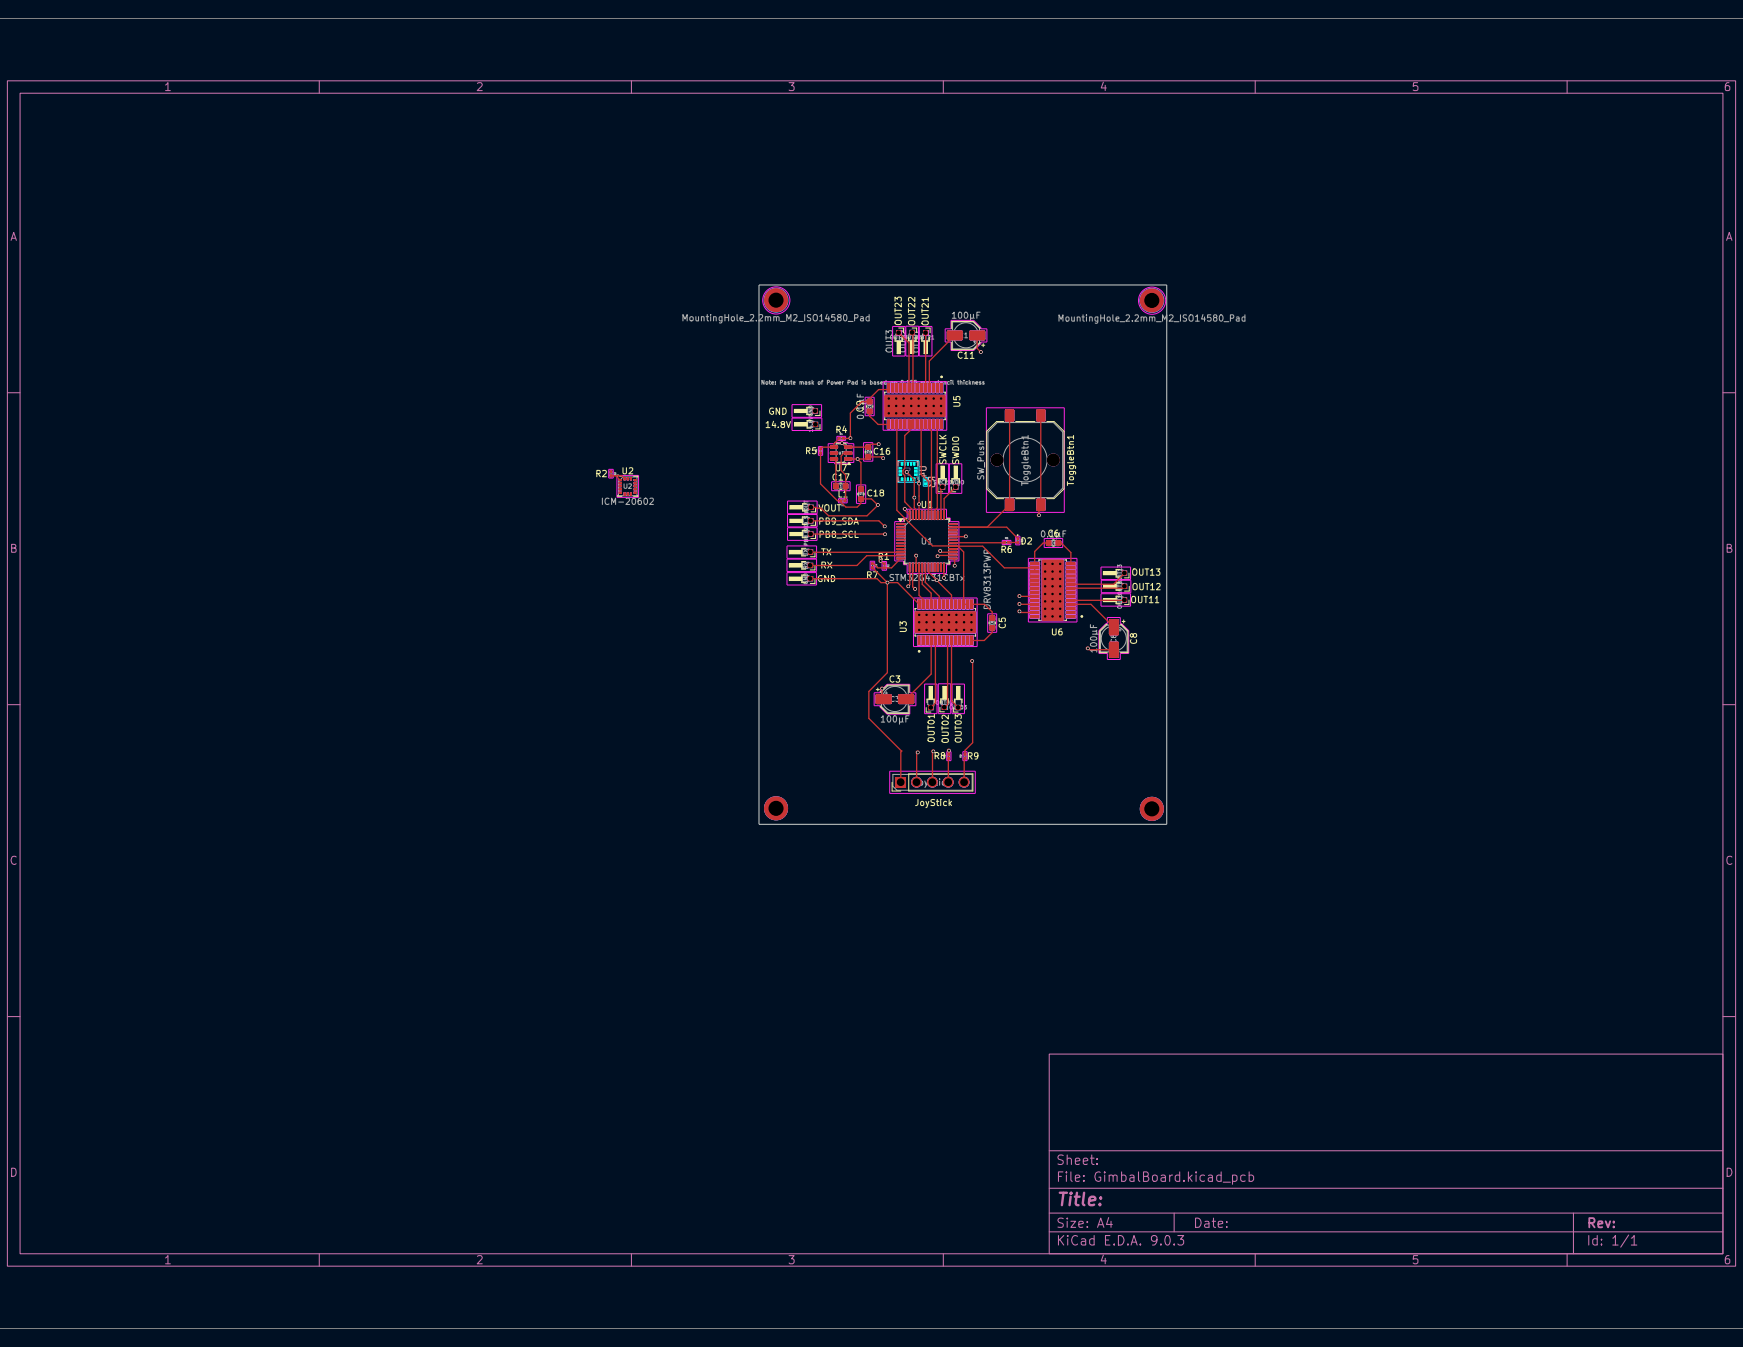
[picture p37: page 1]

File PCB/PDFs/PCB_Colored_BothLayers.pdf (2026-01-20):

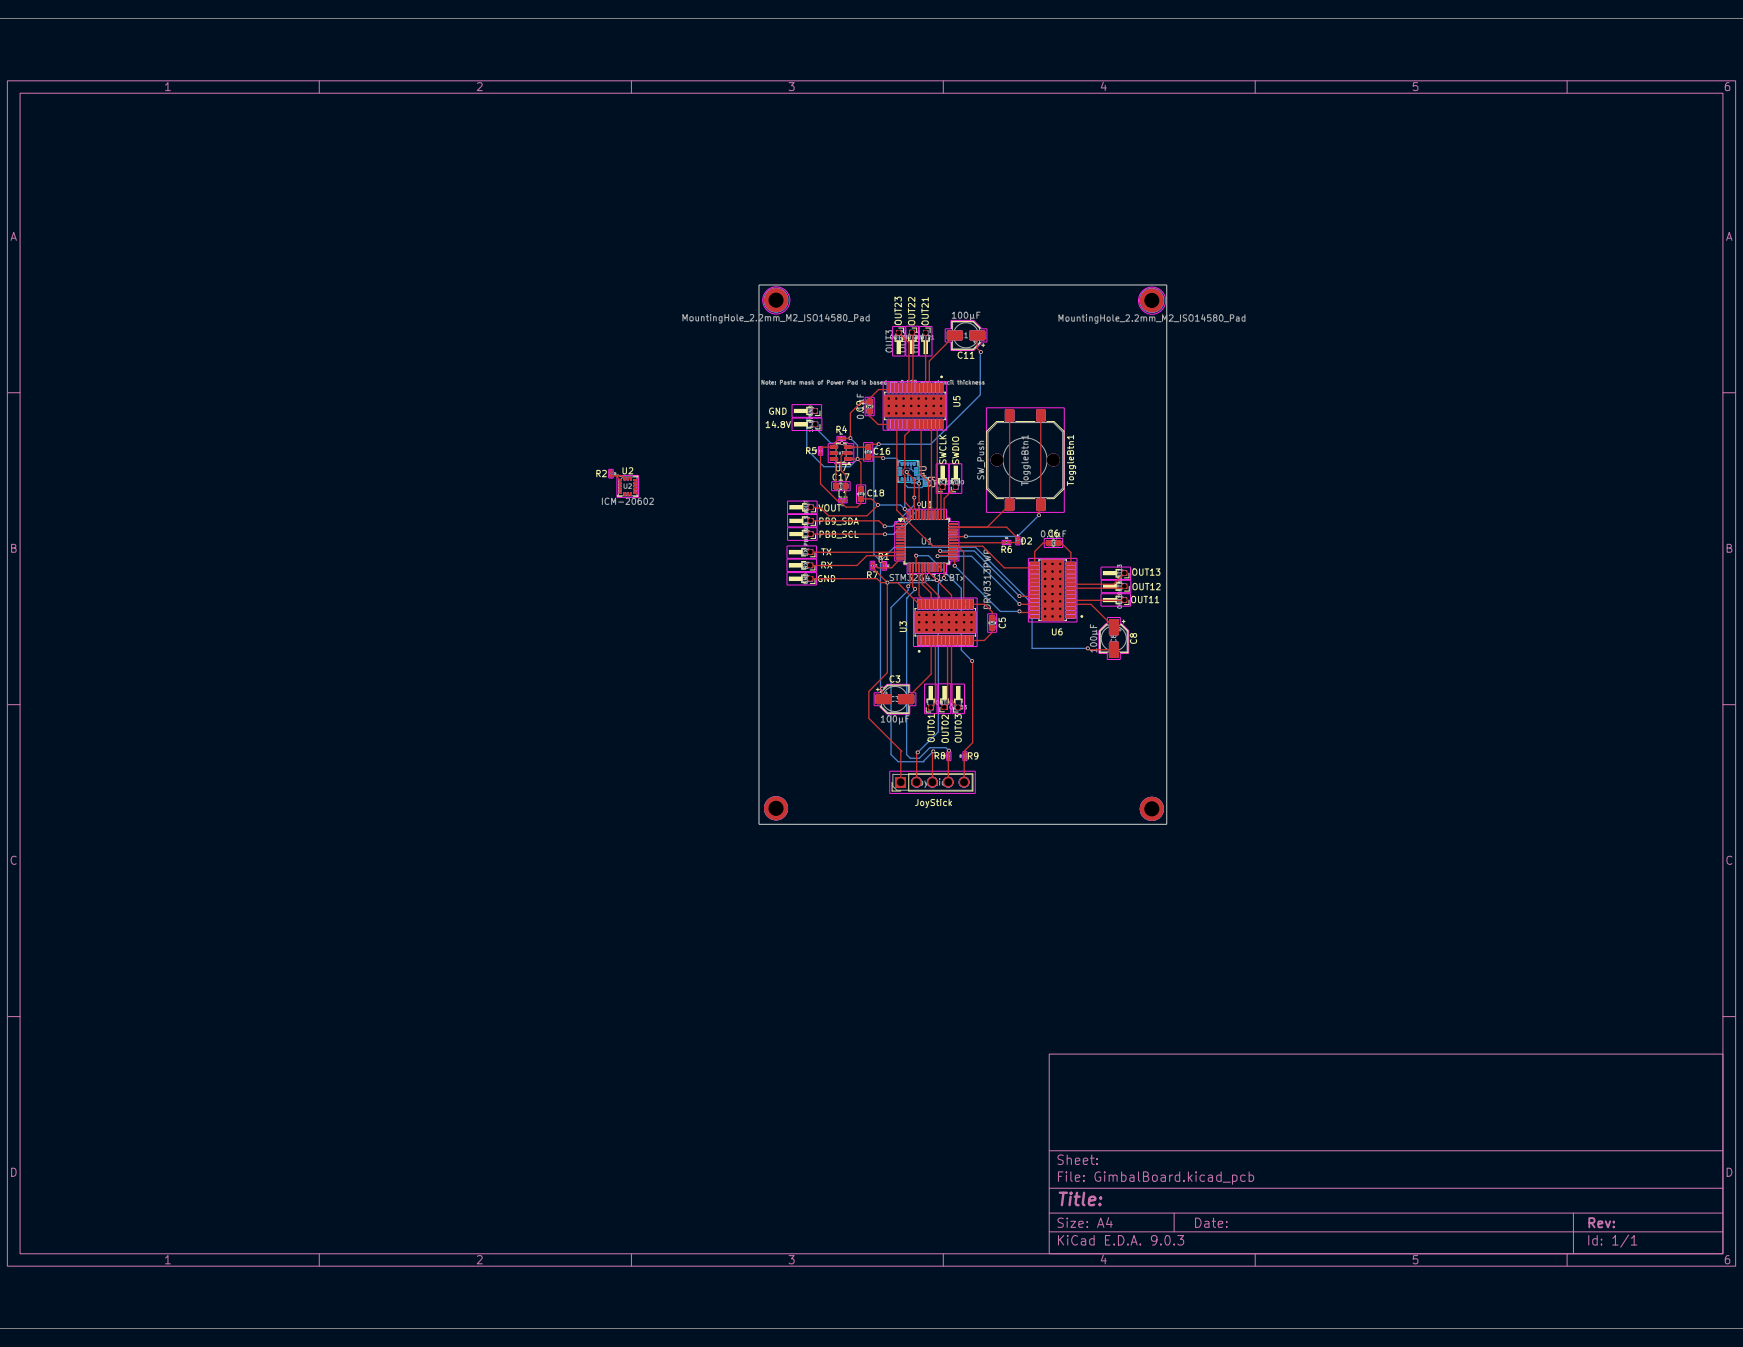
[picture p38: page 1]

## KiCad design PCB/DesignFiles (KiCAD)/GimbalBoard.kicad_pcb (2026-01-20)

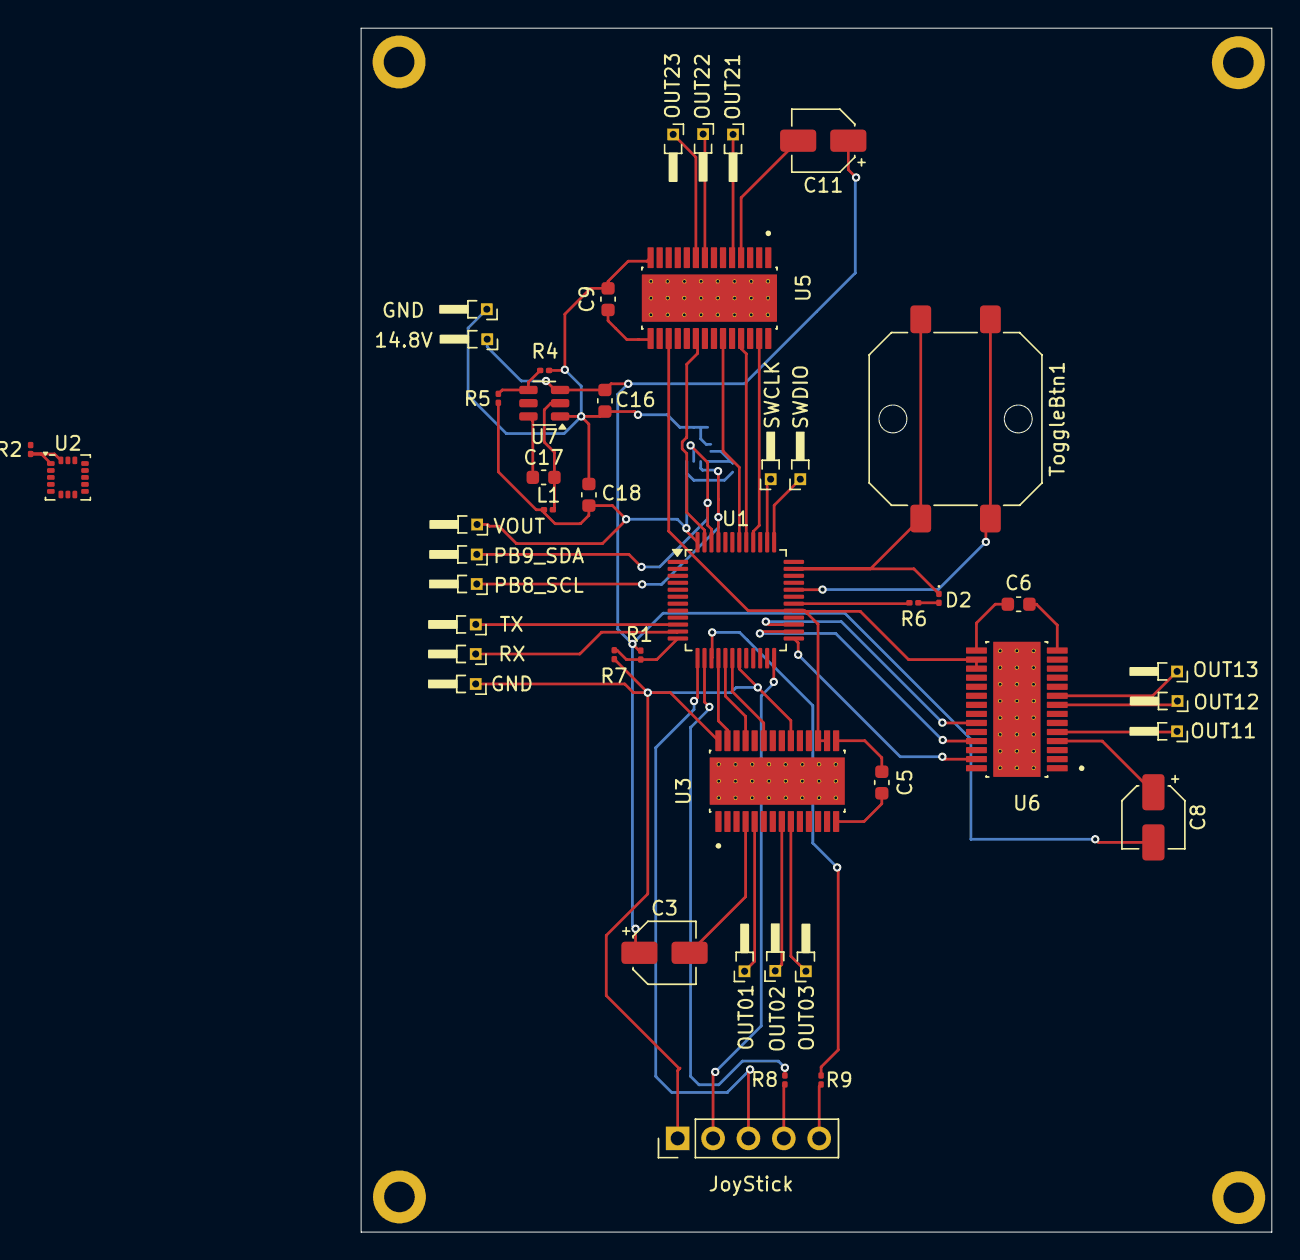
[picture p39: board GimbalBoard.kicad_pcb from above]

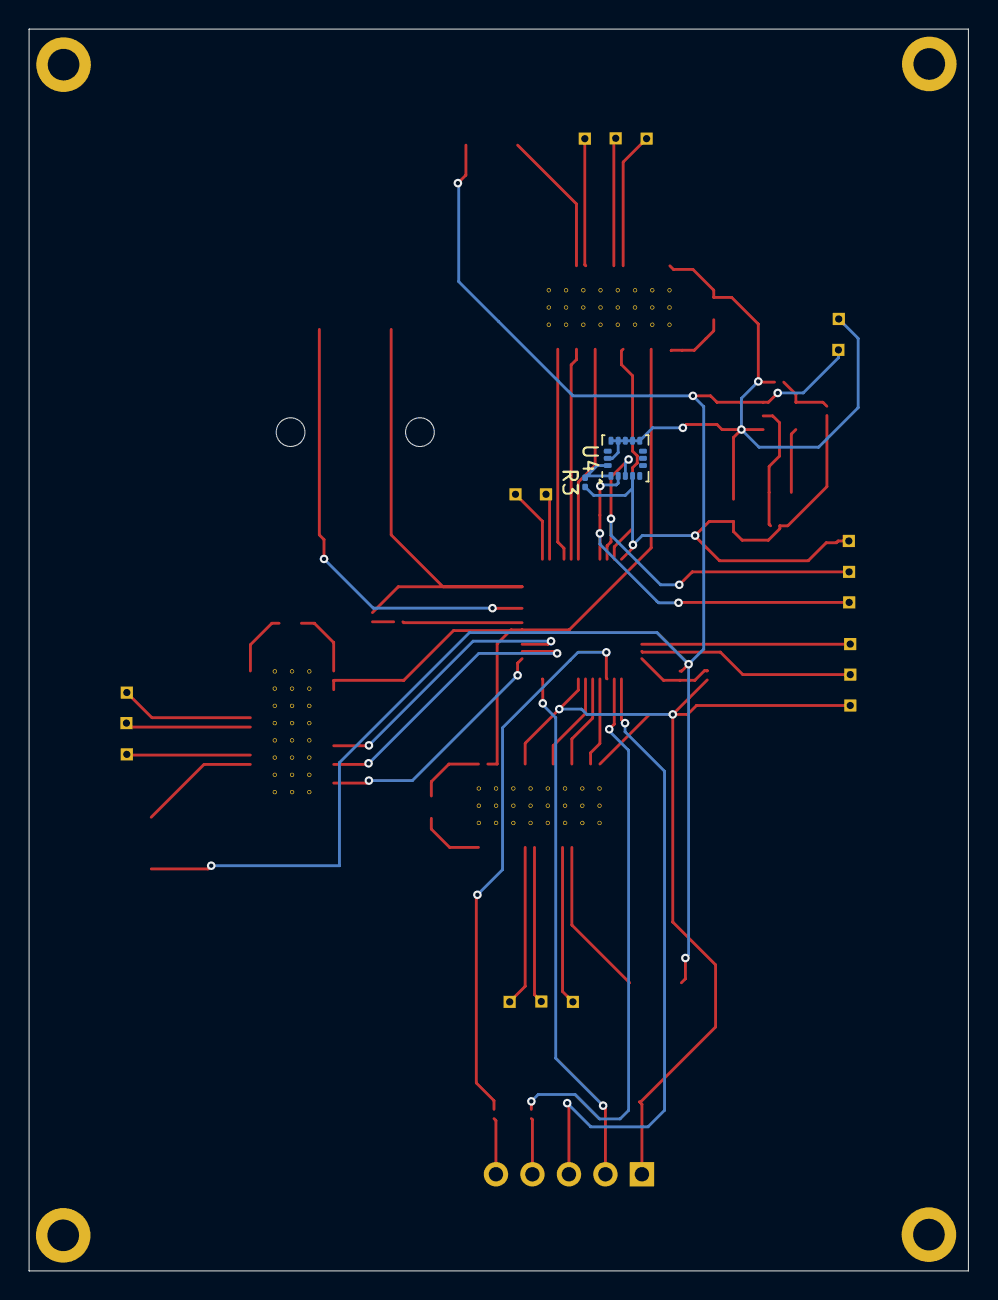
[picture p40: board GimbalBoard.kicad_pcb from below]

Board: 2 copper layers, 65.4 x 86.4 mm, 48 parts (2 on the bottom side), 46 nets.

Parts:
14.8V: TX; PinHeader_1x01_P1.00mm_Horizontal
C3, C8, C11: 100μF; CP_Elec_4x3
C5, C6, C9: 0.1μF; C_0603_1608Metric
C16, C17, C18: 10μF; C_0603_1608Metric
D2: LED; LED_0201_0603Metric
GND: RX; PinHeader_1x01_P1.00mm_Horizontal
GND#2: TX; PinHeader_1x01_P1.00mm_Horizontal
JoyStick: Conn_01x05_Pin; PinHeader_1x05_P2.54mm_Vertical
L1: 10μH; L_0201_0603Metric
OUT01, OUT11, OUT21: OUT1; PinHeader_1x01_P1.00mm_Horizontal
OUT02, OUT12, OUT22: OUT2; PinHeader_1x01_P1.00mm_Horizontal
OUT03, OUT13, OUT23: OUT3; PinHeader_1x01_P1.00mm_Horizontal
PB8_SCL: RX; PinHeader_1x01_P1.00mm_Horizontal
PB9_SDA: TX; PinHeader_1x01_P1.00mm_Horizontal
R1: 100KΩ; R_0201_0603Metric
R2, R3: 2.2KΩ; R_0201_0603Metric
R4, R7: 10KΩ; R_0201_0603Metric
R5: 45.3KΩ; R_0201_0603Metric
R6, R8, R9: 1KΩ; R_0201_0603Metric
RX: RX; PinHeader_1x01_P1.00mm_Horizontal
SWCLK: SWCLK; PinHeader_1x01_P1.00mm_Horizontal
SWDIO: SWDIO; PinHeader_1x01_P1.00mm_Horizontal
TX: TX; PinHeader_1x01_P1.00mm_Horizontal
ToggleBtn1: SW_Push; SW_Push_1P1T_NO_CK_PTS125Sx85PSMTR
U1: STM32G431CBTx; LQFP-48_7x7mm_P0.5mm
U2, U4: ICM-20602; LGA-16_3x3mm_P0.5mm_LayoutBorder3x5y
U3, U5, U6: DRV8313PWP; SOP65P640X120-29N
U7: TPS54302; SOT-23-6
VOUT: TX; PinHeader_1x01_P1.00mm_Horizontal

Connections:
GND: C5.1, C6.1, C9.1, C16.2, C18.2, D2.1 (K), GND.1, GND#2.1, JoyStick.1, R4.2, R7.2, ToggleBtn1.2, U1.19 (VSSA), U1.23 (VSS), U1.35 (VSS), U1.47 (VSS), U2.4 (SAO/SD0), U2.9 (GND), U2.10 (GND), U2.11 (GND), U2.12 (GND), U2.13 (GND), U2.15 (GND), U3.14 (GND), U3.20 (GND), U3.28 (GND), U4.9 (GND), U4.10 (GND), U4.11 (GND), U4.12 (GND), U4.13 (GND), U4.15 (GND), U5.14 (GND), U5.20 (GND), U5.28 (GND), U6.14 (GND), U6.20 (GND), U6.28 (GND), U7.1 (GND)
NSLEEP: U1.29 (PB15), U3.16 (~RESET), U3.17 (~SLEEP), U5.16 (~RESET), U5.17 (~SLEEP), U6.16 (~RESET), U6.17 (~SLEEP)
unnamed: D2.2 (A), R6.2
unnamed: TX.1, U1.10 (PA2)
unnamed: RX.1, U1.11 (PA3)
unnamed: SWDIO.1, U1.37 (PA13)
unnamed: SWCLK.1, U1.38 (PA14)
unnamed: JoyStick.4, R8.1
unnamed: JoyStick.5, R9.1
unnamed: OUT01.1, U3.5 (OUT1)
unnamed: OUT02.1, U3.8 (OUT2)
unnamed: OUT03.1, U3.9 (OUT3)
unnamed: OUT11.1, U6.5 (OUT1)
unnamed: OUT12.1, U6.8 (OUT2)
unnamed: OUT13.1, U6.9 (OUT3)
unnamed: OUT21.1, U5.5 (OUT1)
unnamed: OUT22.1, U5.8 (OUT2)
unnamed: OUT23.1, U5.9 (OUT3)
unnamed: R1.2, R7.1, U1.12 (PA4)
unnamed: R6.1, U1.30 (PA8)
unnamed: R2.2, U2.1 (VDDIO), U2.16 (VDD)
unnamed: C5.2, U3.15 (V3P3)
unnamed: R3.2, U4.1 (VDDIO), U4.16 (VDD)
unnamed: C9.2, U5.15 (V3P3)
unnamed: C6.2, U6.15 (V3P3)
unnamed: C17.1, U7.6 (BOOT)
unnamed: R4.1, R5.2, U7.4 (FB)
unnamed: C17.2, L1.1, U7.2 (SW)
PB8_SCL: PB8_SCL.1, U1.45 (PB8), U2.2 (SCL/SPC), U4.2 (SCL/SPC)
PB9_SDA: PB9_SDA.1, U1.46 (PB9), U2.3 (SDA/SDI), U4.3 (SDA/SDI)
SW_STICK: JoyStick.3, U1.13 (PA5)
TIM1_0: U1.16 (PB0), U3.27 (IN1)
TIM1_1: U1.17 (PB1), U3.25 (IN2)
TIM1_2: U1.18 (PB2), U3.23 (IN3)
TIM2_0: U1.40 (PB3), U5.27 (IN1)
TIM2_1: U1.41 (PB4), U5.25 (IN2)
TIM2_2: U1.42 (PB5), U5.23 (IN3)
TIM3_0: U1.25 (PB11), U6.27 (IN1)
TIM3_1: U1.26 (PB12), U6.25 (IN2)
TIM3_2: U1.27 (PB13), U6.23 (IN3)
Toggle: ToggleBtn1.1, U1.32 (PA10)
VIN: 14.8V.1, C3.1, C8.2, C11.1, C16.1, R1.1, U7.3 (VIN)
VM: C3.2, C8.1, C11.2, U3.4 (VM), U3.11 (VM), U5.4 (VM), U5.11 (VM), U6.4 (VM), U6.11 (VM)
VOUT: C18.1, JoyStick.2, L1.2, R2.1, R3.1, R5.1, U1.21 (VDDA), U1.24 (VDD), U1.36 (VDD), U1.48 (VDD), U4.4 (SAO/SD0), VOUT.1
VRx: R8.2, U1.14 (PA6)
VRy: R9.2, U1.15 (PA7)

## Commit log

2026-01-18 Added bom and journal
    [BOM.csv, BOM.xlsx]
2026-01-18 Aditionals and Edits
    [DRV8313PWP.step, GimbalBoard.kicad_pcb, GimbalBoard.kicad_sch]
2026-01-20 pcb image
2026-02-02 wiring diagram
    [BOM.csv, Render.blend]
2026-02-02 edit on wiring diagram
2026-02-02 Bom edit
2026-02-03 edit to BOM & delivery
    [BOM.csv, Render.blend]
